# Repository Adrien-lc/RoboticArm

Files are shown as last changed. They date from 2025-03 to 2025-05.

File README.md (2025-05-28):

# Robotic Arm






<p float="left">
  
</p>

## Overview

This Robotic Arm is designed to perform simple to complex manipulative tasks, enabling the implementation of AI models. The arm is scaled to human proportions and designed to be cost-effective, with all parts 3D printed.

The arm can be used both vertically, like a human arm, or horizontally, like a traditional DOF robot. It only needs to be connected to a computer through the USB-C port.

<p float="left">
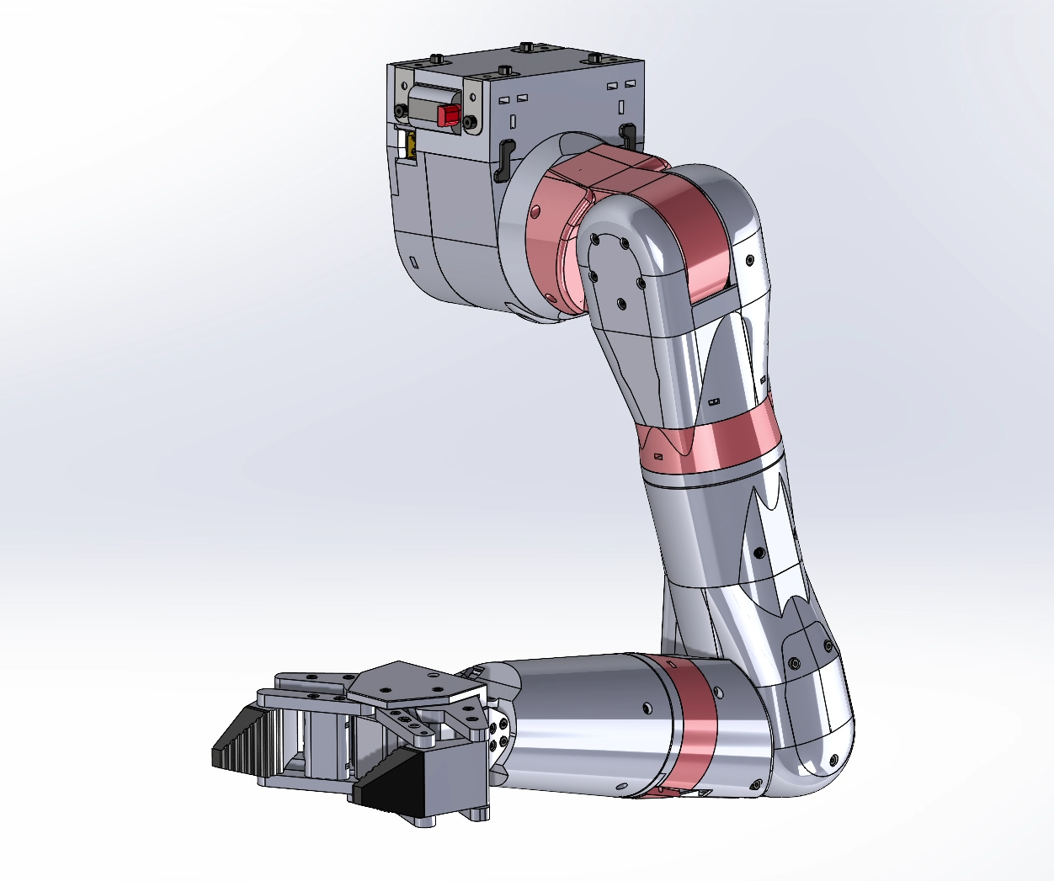
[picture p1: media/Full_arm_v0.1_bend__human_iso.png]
  
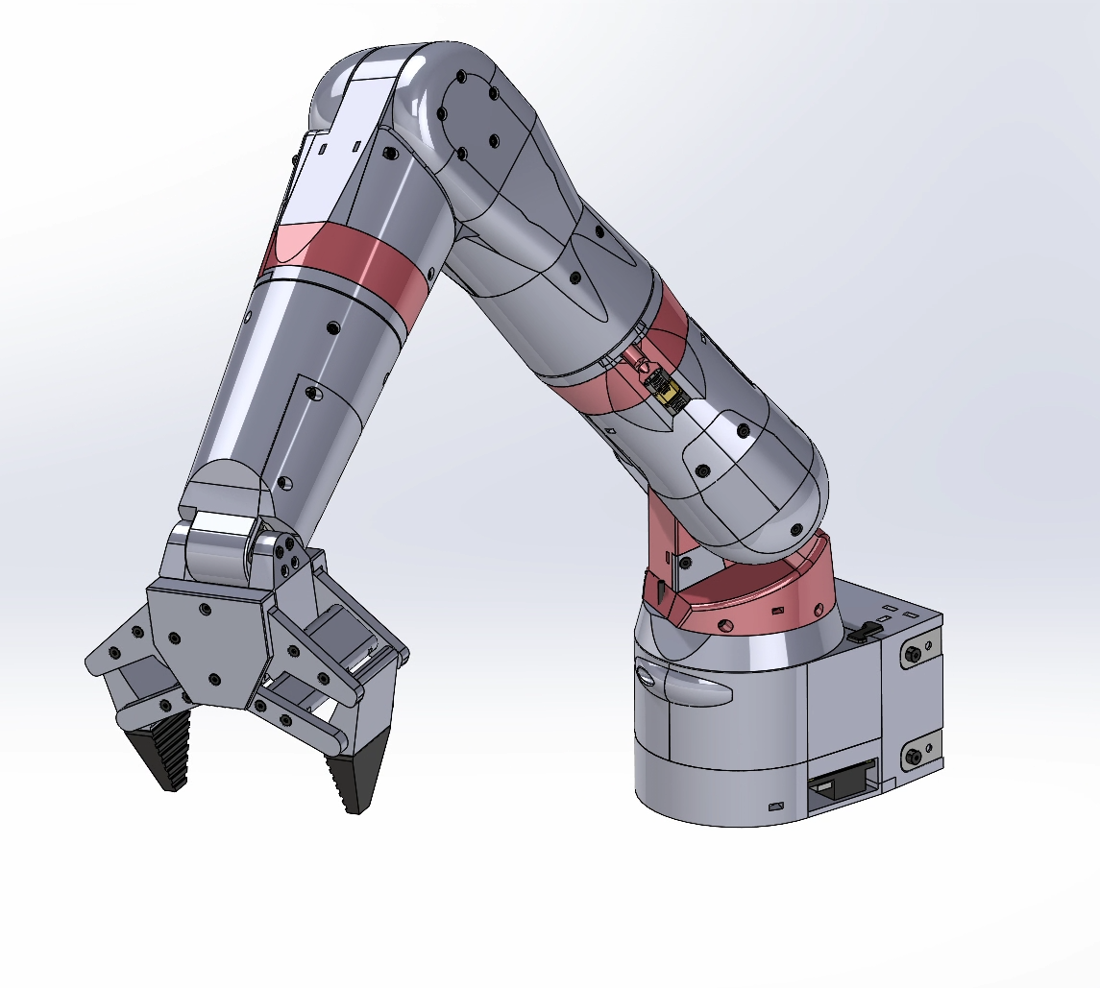
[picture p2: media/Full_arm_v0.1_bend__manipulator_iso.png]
  
</p>

## Sourcing Parts

Detailed part costs and links are shown below. Some links may provide more than the necessary quantity. You can find the complete Bill of Materials (BOM) in the repository files. 

Please note, you need to add the cost of the 3D printed parts to this list.

> Only EU costs and availability have been calculated.

### Parts to buy : 

| Description | Supplier | Quantity | Unit Price (EUR) | Total Price (EUR) | Link |
|---|---|---|---|---|---|
| Servo Feetech STS3215 | Alibaba | 7 | 13 | 91 | [Alibaba](https://docs.google.com/spreadsheets/d/1NSq1UUoz3DjgiEBvVC6gFn5Jqz1jVz-hb513ZOTMuxQ/edit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) |
| Waveshare Serial Bus Servo Driver Board | Amazon | 1 | 11.99 | 11.99 | [Amazon](https://www.amazon.fr/dp/B0CJ6TP3TP) |
| LiPo Roaringtop 2200mAh 35C, 2pcs | Amazon | 1 | 32.1 | 32.1 | [Amazon](https://www.amazon.fr/dp/B08H82KFS6/ref=twister_B09YHFFBK1?_encoding=UTF8&th=1) |
| Universal Lithium Grease | Amazon | 1 | 7.99 | 7.99 | [Amazon](https://www.amazon.fr/dp/B008ETHDPO) |
| Hex Screw M3 Socket Cap, Box | Amazon | 1 | 10.59 | 10.59 | [Amazon](https://www.amazon.fr/dp/B093GNHWKR) |
| Bearing 20x27x4, 6704 2RS, 5pcs | Aliexpress | 1 | 4.61 | 4.61 | [Aliexpress](https://fr.aliexpress.com/item/1005006822777675.html) |
| Bearing 8x16x5, 688ZZ, 10pcs | Aliexpress | 1 | 1.75 | 1.75 | [Aliexpress](https://fr.aliexpress.com/item/1005007235103277.html) |
| Bearing 40x52x7, 6808-2RS, 2pcs | Aliexpress | 2 | 3.51 | 7.02 | [Aliexpress](https://fr.aliexpress.com/item/1005007420073930.html) |
| Bearing 15x21x4, 6702ZZ, ABEC 1, 10pcs | Aliexpress | 2 | 3.43 | 6.86 | [Aliexpress](https://fr.aliexpress.com/item/4000909621264.html) |
| Bearing 50x65x7, 6810-2RS, 2pcs | Aliexpress | 2 | 5.09 | 10.18 | [Aliexpress](https://fr.aliexpress.com/item/1005007420073930.html) |
| Wire AWG16 3 Core, 3m | Aliexpress | 1 | 10.39 | 10.39 | [Aliexpress](https://fr.aliexpress.com/item/1005006405984242.html) |
| Hex Socket M3 Countersunk Flat Head Screw, 8mm, 50pcs | Aliexpress | 1 | 1.66 | 1.66 | [Aliexpress](https://fr.aliexpress.com/item/4001199728978.html) |
| Hex Socket M3 Countersunk Flat Head Screw, 10mm, 50pcs | Aliexpress | 1 | 1.75 | 1.75 | [Aliexpress](https://fr.aliexpress.com/item/4001199728978.html) |
| Hex Socket M3 Countersunk Flat Head Screw, 12mm, 50pcs | Aliexpress | 1 | 1.84 | 1.84 | [Aliexpress](https://fr.aliexpress.com/item/4001199728978.html) |
| Hex Socket M3 Countersunk Flat Head Screw, 16mm, 50pcs | Aliexpress | 1 | 2.04 | 2.04 | [Aliexpress](https://fr.aliexpress.com/item/4001199728978.html) |
| Dowel Pin M2, 20mm, 20pcs | Aliexpress | 1 | 1.3 | 1.3 | [Aliexpress](https://fr.aliexpress.com/item/1005007218328914.html) |
| Dowel Pin M3, 30mm, 20pcs | Aliexpress | 1 | 2.69 | 2.69 | [Aliexpress](https://fr.aliexpress.com/item/1005007023343232.html) |
| Dowel Pin M3, 25mm, 20pcs | Aliexpress | 1 | 2.55 | 2.55 | [Aliexpress](https://fr.aliexpress.com/item/1005007023343232.html) |
| Dowel Pin M3, 16mm, 20pcs | Aliexpress | 1 | 2.06 | 2.06 | [Aliexpress](https://fr.aliexpress.com/item/1005007023343232.html) |
| AMASS MR30 Pair Male+Female, 10pcs | Aliexpress | 1 | 6.61 | 6.61 | [Aliexpress](https://fr.aliexpress.com/item/1005005485789207.html) |
| Heat Shrink Tube, Box 127pcs | Aliexpress | 1 | 2.24 | 2.24 | [Aliexpress](https://fr.aliexpress.com/item/1005001787291963.html) |
| Allen Hexagon Head Screws M4 20mm, 10pcs | Aliexpress | 1 | 1.36 | 1.36 | [Aliexpress](https://fr.aliexpress.com/item/32442183034.html) |
| Allen Hexagon Head Screws M4 40mm, 10pcs | Aliexpress | 1 | 1.88 | 1.88 | [Aliexpress](https://fr.aliexpress.com/item/32442183034.html) |
| M4 Nuts Hexa, 25pcs | Aliexpress | 1 | 1.38 | 1.38 | [Aliexpress](https://fr.aliexpress.com/item/32977174437.html) |
| Hex Socket M2.5 Countersunk Flat Head Screw, 12mm, 50pcs | Aliexpress | 1 | 1.65 | 1.65 | [Aliexpress](https://fr.aliexpress.com/item/4001199728978.html) |
| Hex Socket M3 Countersunk Flat Head Screw, 25mm, 50pcs | Aliexpress | 1 | 2.59 | 2.59 | [Aliexpress](https://fr.aliexpress.com/item/4001199728978.html) |
| Hex Socket M3 Socketcap Head Screw, 45mm, 50pcs | Aliexpress | 1 | 3.80 | 3.80 | [Aliexpress](https://fr.aliexpress.com/item/32442183034.html) |
| XT60 Male Connector | Aliexpress | 1 | 1.59 | 1.59 | [Aliexpress](https://fr.aliexpress.com/item/1005006840459578.html) |
| Lipo Battery Charger | Aliexpress | 1 | 5.01 | 5.01 | [Aliexpress](https://fr.aliexpress.com/item/1005007620618797.html) |
| MR30 male and female connector, 10pcs | Aliexpress | 1 | 6.59 | 7.99 | [Aliexpress](https://fr.aliexpress.com/item/1005005485789207.html) |
| **Total** |  |  |  | **246.96** | |

> Make sure the AWG 16, 3-core wire outside diameter is equal to or less than 7mm.

### 3D Printed Parts

All the 3D printed parts can be found in the `/STEP` folder.  For main assembly, open `Bionic_arm.STEP`
Parts have been tested with an Artillery SW-X4 Plus printer.

## Specifications

This arm is first designed as a human arm. It has a 1:1 scale and the same joint amplitude :

- The arm needs to be able to lift a 500g object.
- End-effector position error must be < 1 cm.
- The arm must be able to pick up an object from any orientation within its kinematic workspace.
- Actuator velocity must be fast enough to perform a task at a reasonable speed. Full amplitude < 4s.

### Joint Amplitude:

| Joint | Min  | Max  | Amplitude |
|---|---|---|---|
| Shoulder Y | -90  | 180  | 270 |
| Shoulder X | -20  | 150  | 170 |
| Upper Z | -180 | 90 | 270 |
| Elbow Y | -60  | 110  | 170 |
| Forearm Z  | -90  | 90 | 180 |
| Wrist Y | -60  | 60 | 120 |

A first draft was made in Isaac Sim to determine the required specifications for the actuators:
- Joints were placed in the same positions as a human arm.
- The final robot mass was approximated for each rigid body.
- A 500g load was added to the gripper mass to simulate the payload.

Lula RMPflow controller is used, with different positions given while joint effort and velocity are recorded:

<p float="left">
  
</p>

<p float="left">
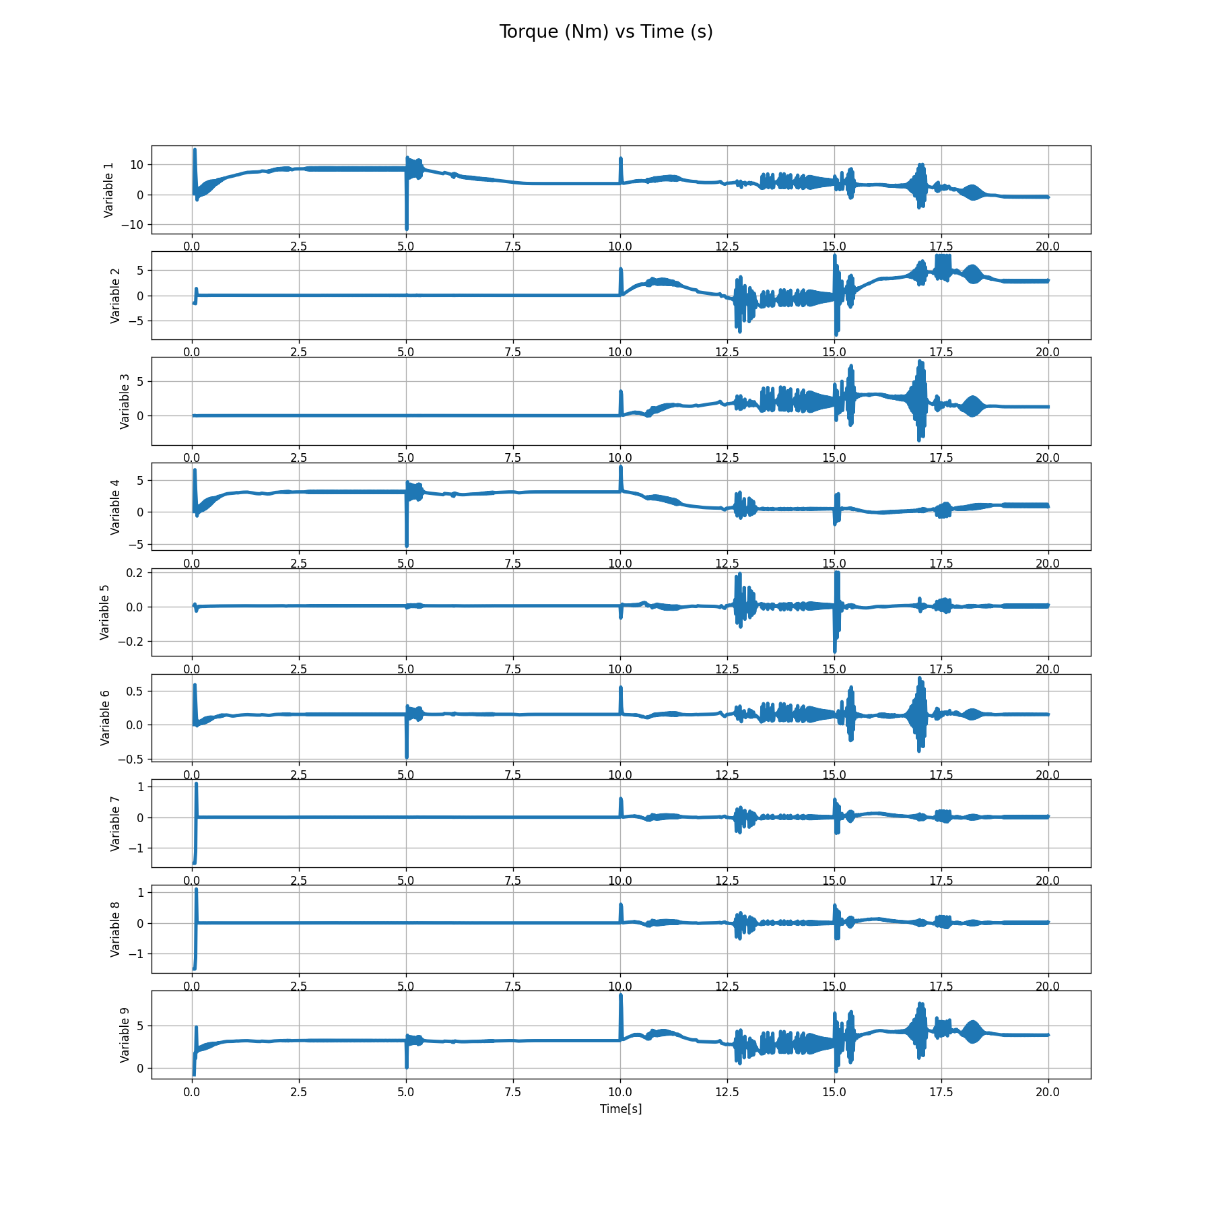
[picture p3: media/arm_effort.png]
  
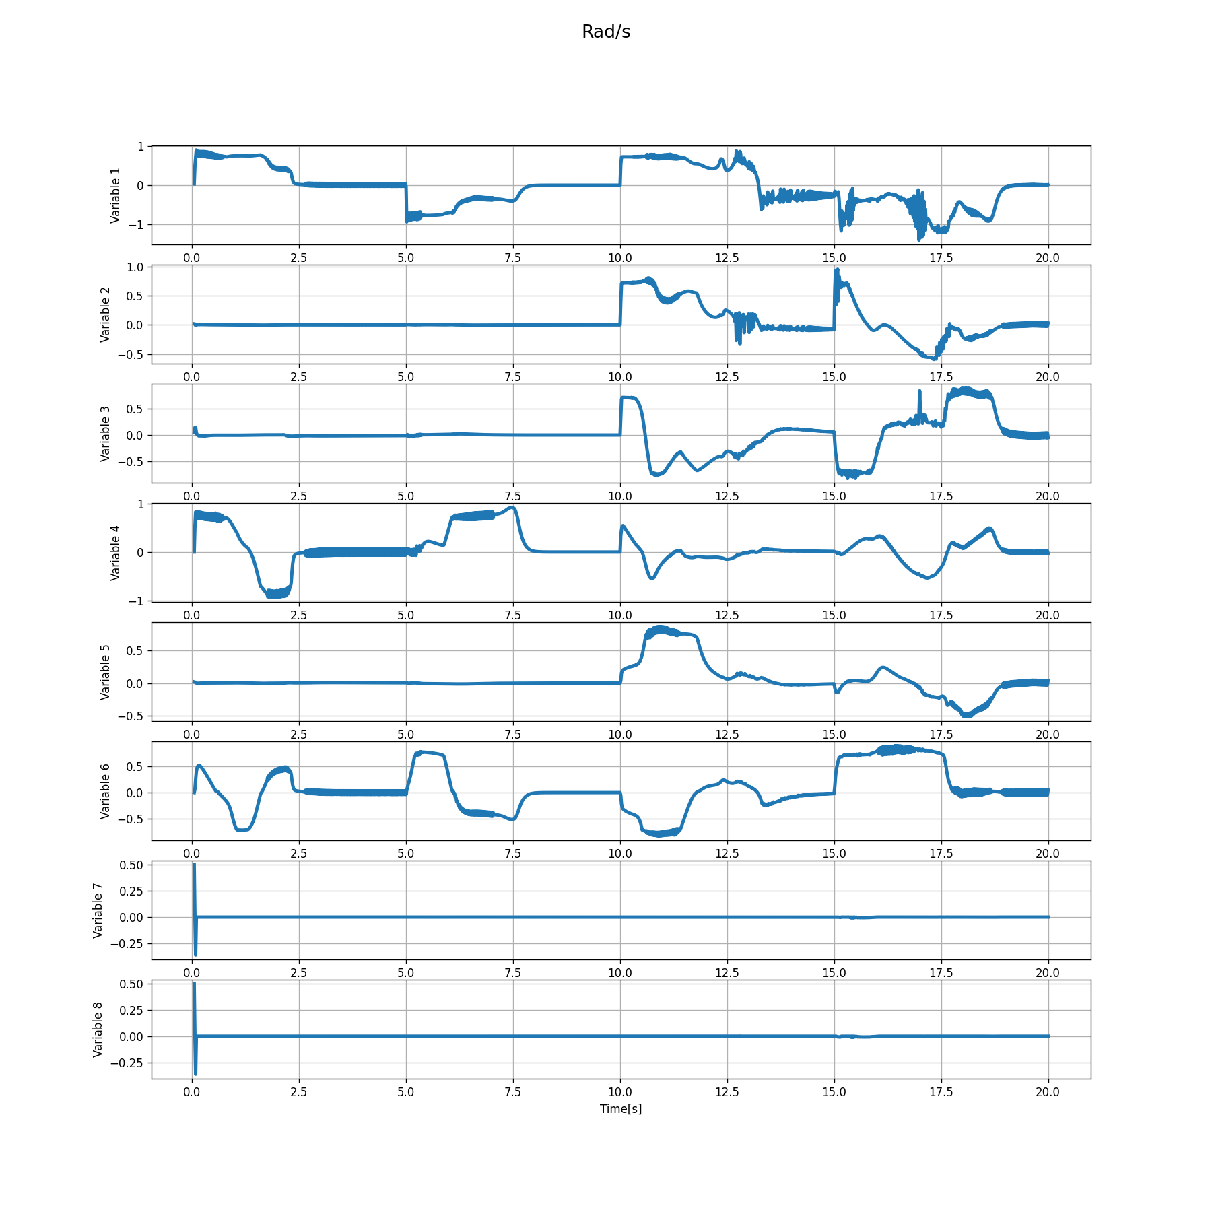
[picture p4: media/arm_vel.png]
  
</p>

### The minimum actuator specifications required are:
- **10 Nm** for the first shoulder joint, **5 Nm** for the rest.
- **≥ 1 rad/s** velocity.

**STS3215** serial servo (3 Nm, 5.5 rad/s, 12V) has been selected for all the joints.

Serial servo allows easier wire management, position/velocity/torque feedback, and features a multi-turn encoder.  
A cycloidal drive will be coupled to the STS servo to achieve the desired torque.

## Cycloid Drive

The gearbox will be used with the Feetech STS3215 servomotors (30 kg·cm, 52 rpm / 5.5 rad/s), with a desired **5:1** gear ratio.  
The shape of the rotor and stator has been tuned using the Python script `cycloid_tuning.py`:  

| Parameter | Value | Description |
|---|---|---|
| R | 36 mm | Pitch radius of fixed ring pins |
| E | 2 mm | Eccentricity offset |
| Rr | 8 mm | Ring pin radius |
| N | 6 | Number of ring pins |
| Sharpness | 6.5 mm  | Pitch angle around stator ring pins |

<p float="left">
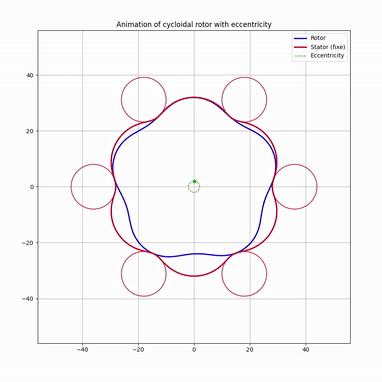
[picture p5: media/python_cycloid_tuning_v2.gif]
  
</p>

This design aims to achieve the best torque distribution and minimize backlash.  
As both rotors and the housing are **3D printed**, a **three-rotor design** has been chosen.  
The Cycloid assembly can be open with `Cycloid_drive_default.STEP` in the `/STEP` folder.  

<p float="left">
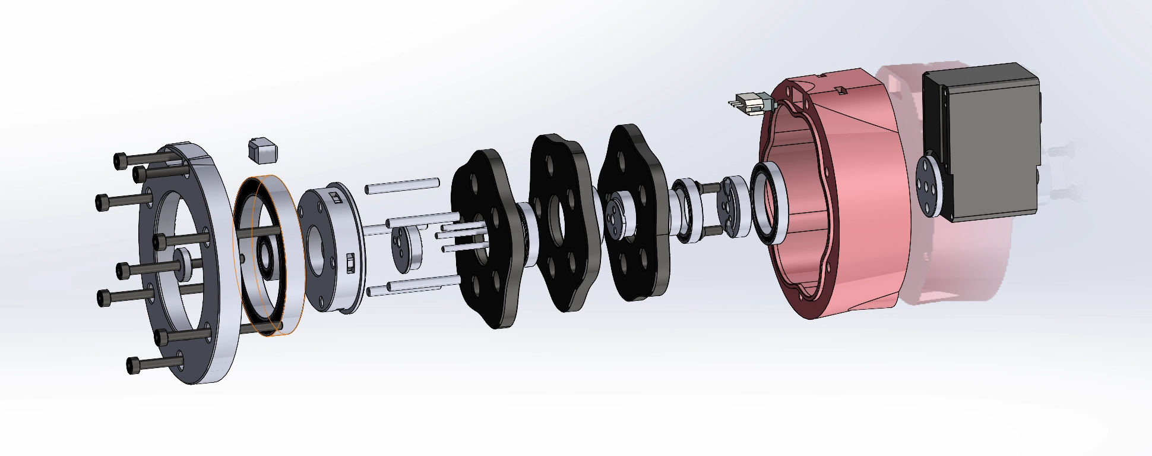
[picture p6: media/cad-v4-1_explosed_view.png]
  
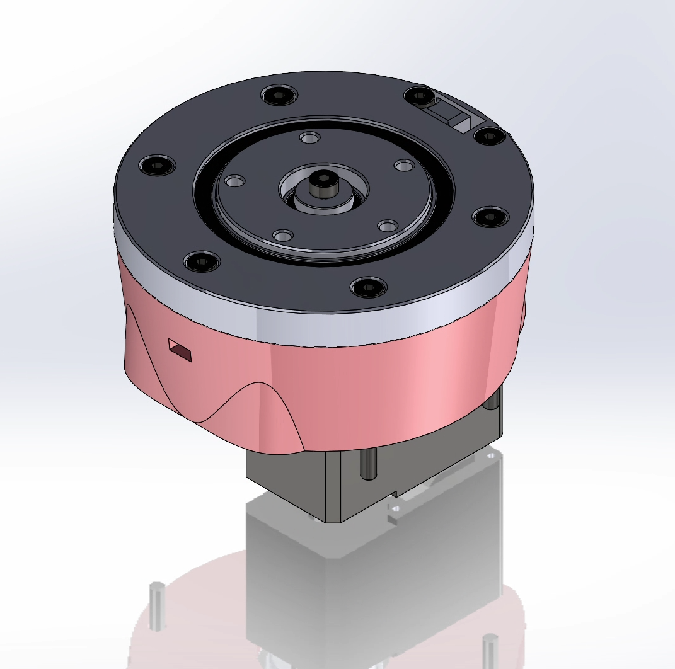
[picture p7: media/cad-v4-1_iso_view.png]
  
</p>

A load test has been conducted to measure output torque, speed, backlash, and efficiency:  

- **Output torque**: 9 Nm  
- **Output velocity**: 1.1 rad/s  
- **Backlash after load**: 0.5°  
- **Efficiency**: (9/3)/5 = **0.6** *(test were conducted with grease)*  

## Assembly

Use the main Assembly File for the main assembly `Bionic_arm.STEP`

**Base component management :**

<p float="left">
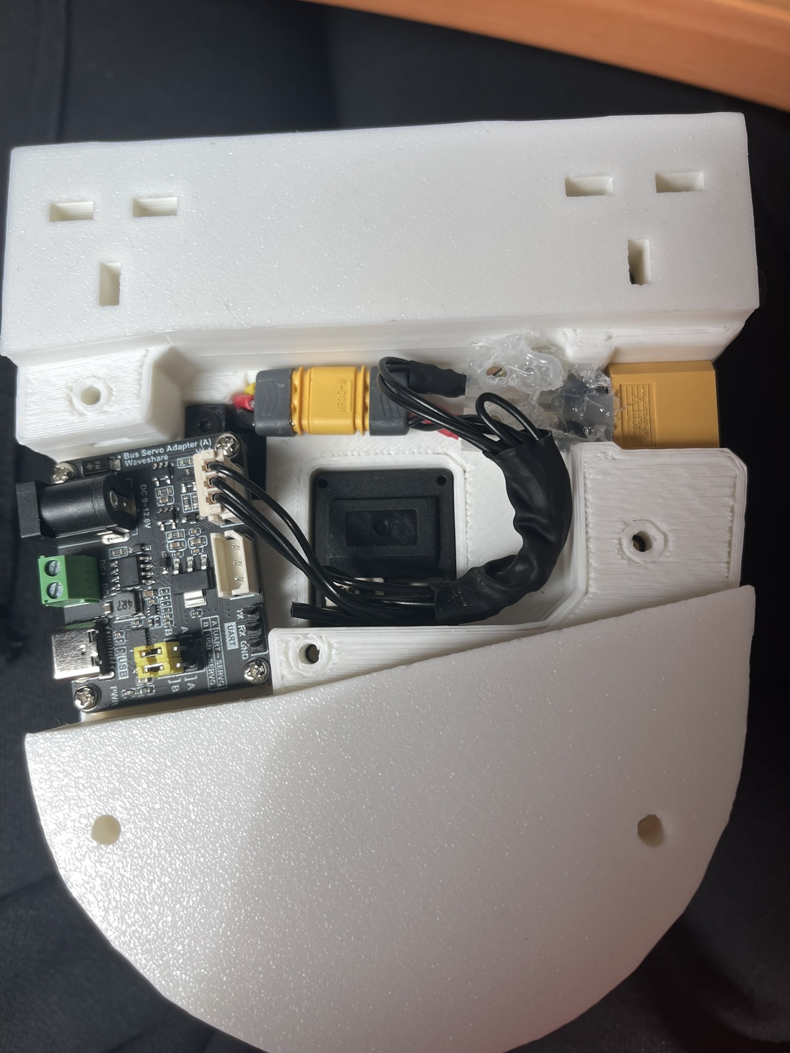
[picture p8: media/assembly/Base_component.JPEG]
  
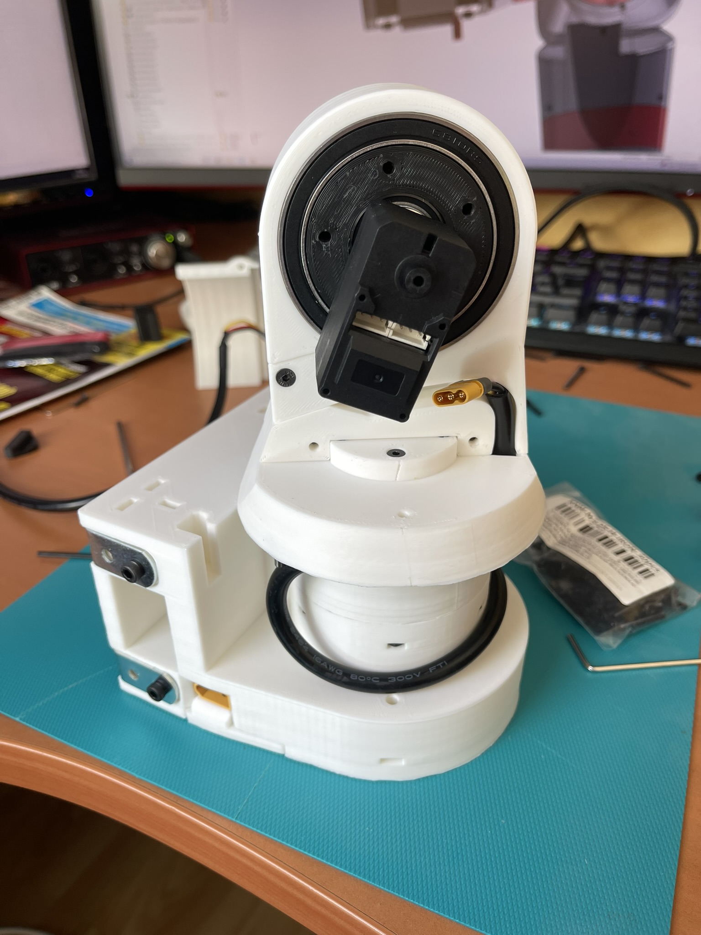
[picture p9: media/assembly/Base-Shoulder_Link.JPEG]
  
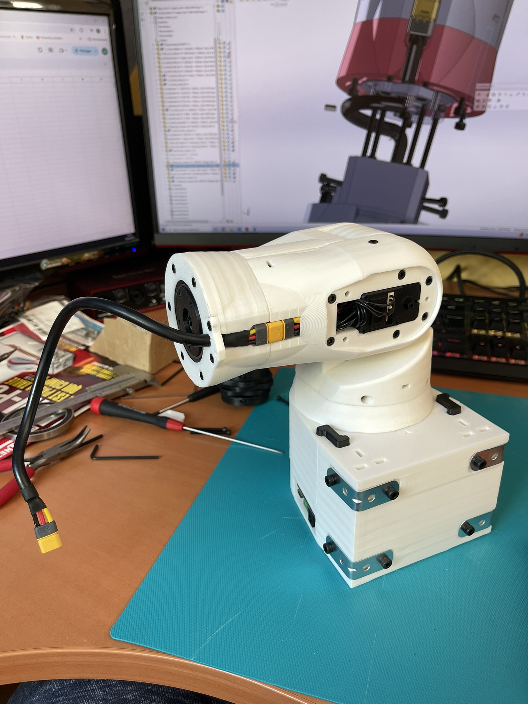
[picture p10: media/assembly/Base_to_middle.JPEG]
  

</p>

> Wire length must be calculated by doing a full amplitude on the joint before soldering it.

**Upper link Wire Management :**

<p float="left">
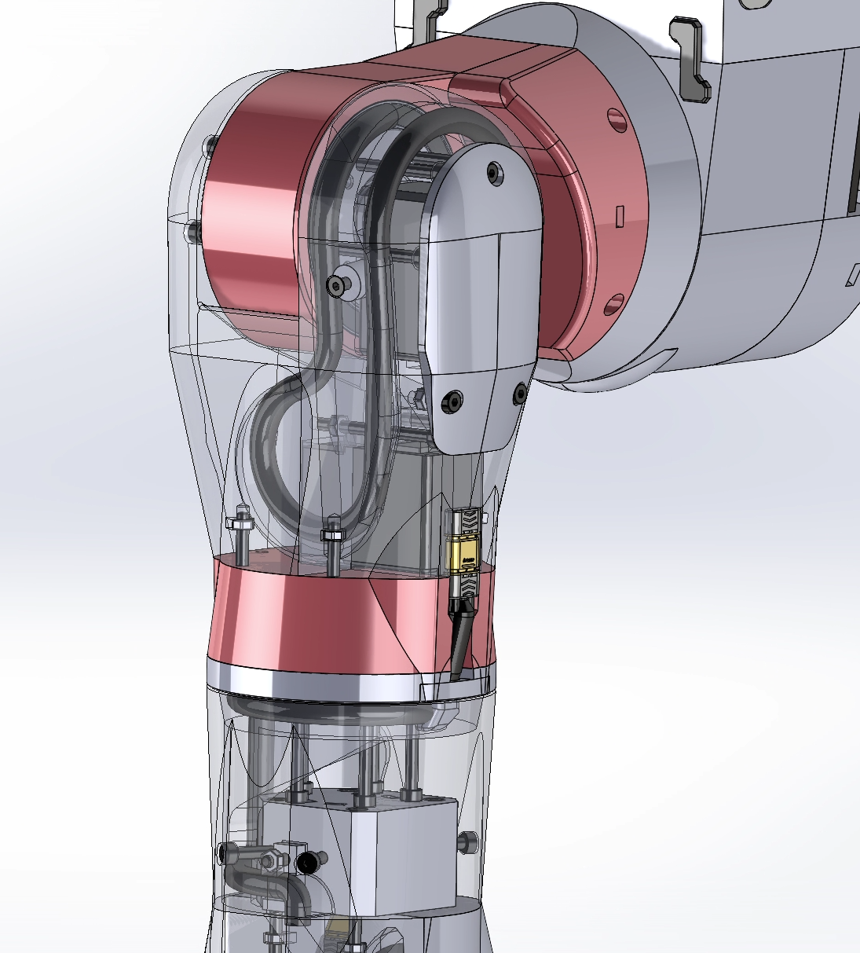
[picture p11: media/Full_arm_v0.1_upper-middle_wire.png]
  
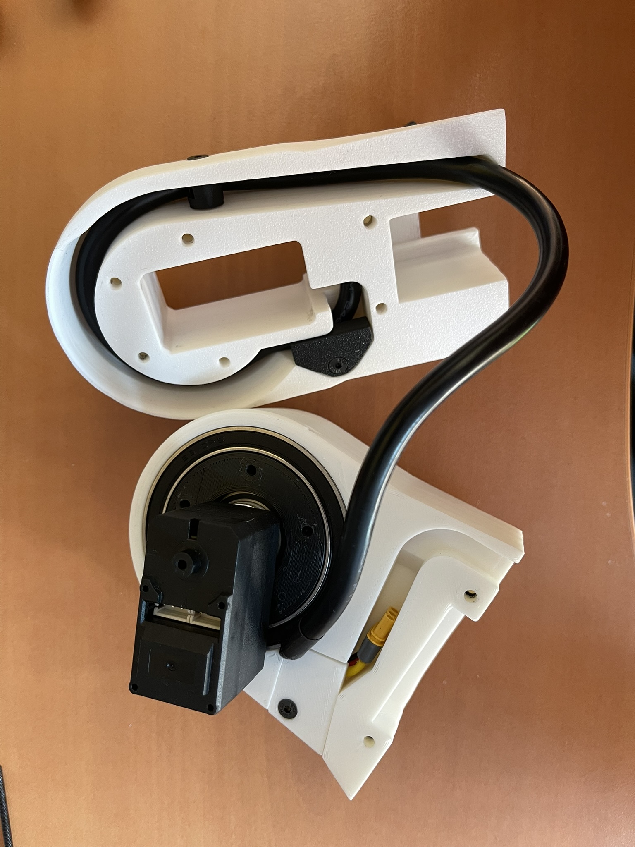
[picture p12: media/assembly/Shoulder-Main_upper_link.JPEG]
  
</p>

> Same wire management for Elbow link

**Fore arm and Wrist link**

<p float="left">
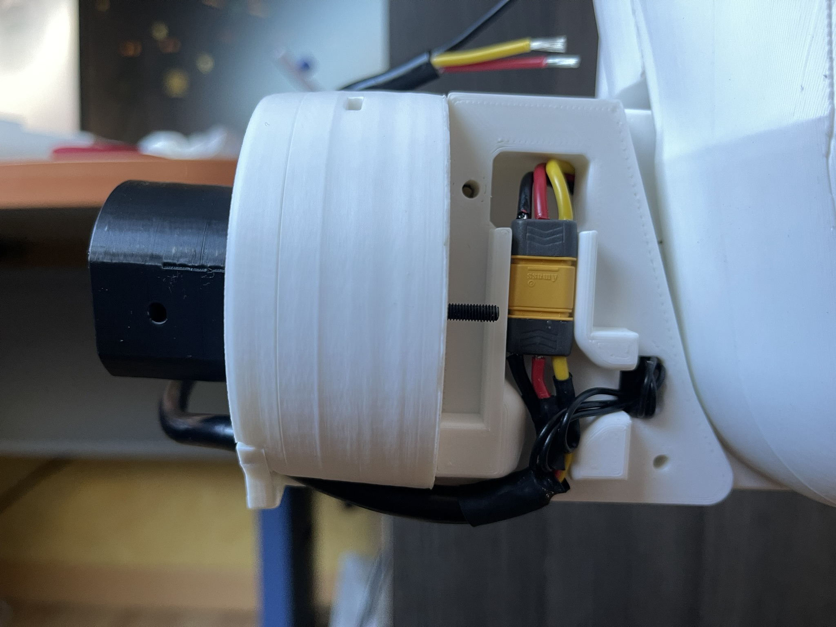
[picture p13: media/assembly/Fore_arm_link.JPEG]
  
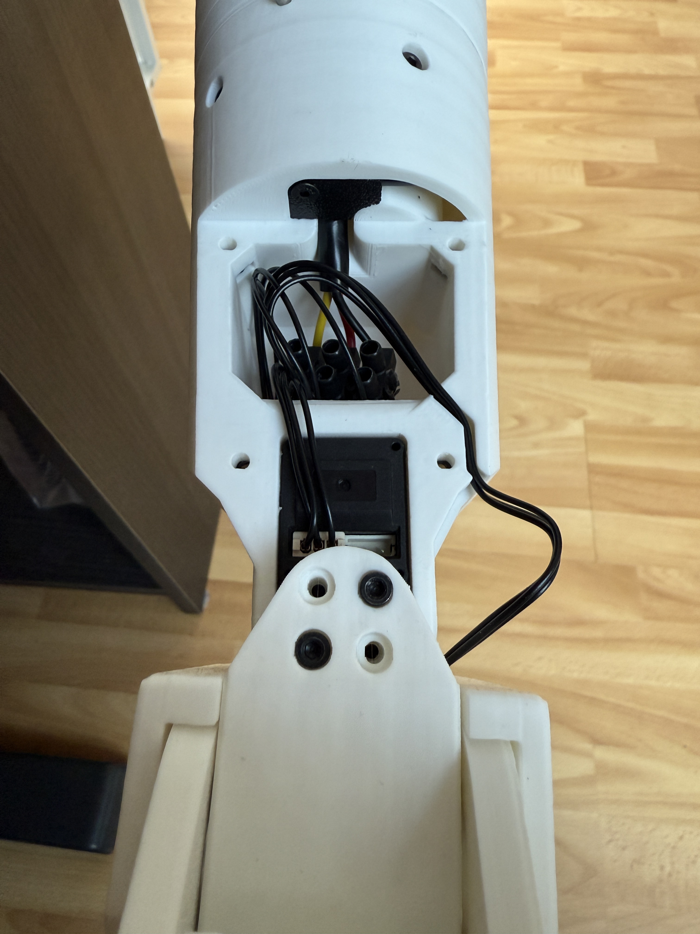
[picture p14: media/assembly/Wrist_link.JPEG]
  
</p>

## IsaacSim

IsaacSim USD file can be found in /isaacSim/USD

### Manipulation Tasks :

In this task, IsaacSim lead the real arm using Lula RMPFlow controller. Current positions and velocities of each joint are sent to the robot in real time :

<p float="left">
  
</p>

### RL (coming soon):

Reinforcement learning model with IsaacLab.

## Software :

<p>Servo motor-related features, such as calibration and serial addressing, were inspired by scripts from <a href="https://github.com/huggingface/lerobot"> Lerobot repository.</a></p>

IsaacSim instance is hosted on a cloud machine, and communication with the local system is handled via a TCP socket, as illustrated in the diagram below. Currently, TCP communication is unidirectional—from IsaacSim to the robot—due to internet latency constraints.

<p float="left">
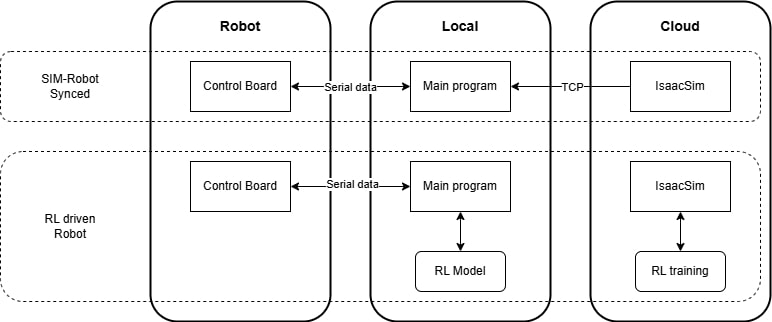
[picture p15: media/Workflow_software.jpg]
  
</p>

The local system runs a main control program , which orchestrates motor connection, calibration routines, overload protection, position safety mechanisms, and TCP communication. All the scripts are written in Python

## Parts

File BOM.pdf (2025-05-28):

ITEM NO. | PART NUMBER | SW-Configuration Name(Configuration Name) | Source | toBuy | DESCRIPTION | QTE
1 | cycloid_housing | default | 3D Print | | | 1
2 | planche | default | home | | | 1
3 | base_housing | default | 3D Print | | | 1
4 | base_axis | default | Printed | | | 1
5 | wire_cover_base_2 | default | Printed | | | 1
6 | cable_pulley | base | Aliexpress | Yes | awg 16 wire, 3 core | 1
7 | roulement | 40x52x7 | Aliexpress | Yes | Bearings | 3
8 | cover_housing | left | Printed | | | 1
9 | cover_housing | right | Printed | | | 1
10 | hex_m3_custom | flat_25mm | Aliexpress | Yes | Screw m3 hexa | 9
11 | nut_m4_hex_custom | default | Aliexpress | Yes | Nut m4 hexa | 12
12 | hex_m4_custom | socketcap_20mm | Aliexpress | Yes | screw M4 hexa | 4
13 | bracket_30x30 | default | | Yes | steel bracket 30x30m m4 | 4
14 | hex_m4_custom | socketcap_40mm | Aliexpress | Yes | screw M4 hexa | 4
15 | hex_m4_custom | socketcap_16mm | Aliexpress | Yes | screw M4 hexa | 4
16 | hex_m3_custom | socketcap_25mm | Aliexpress | Yes | Screw m3 hexa | 10
17 | nut_m3_hex_custom | default | Aliexpress | Yes | Nut hex M3 | 123
18 | hex_m3_custom | socketcap_20mm | Aliexpress | Yes | Screw m3 hexa | 14
19 | wire_cover_base | default | 3D Print | | | 1
20 | hex_m3_custom | flat_16mm | Aliexpress | Yes | Screw m3 hexa | 20
21 | hex_m3_custom | socketcap_30mm | Aliexpress | Yes | Screw m3 hexa | 6
22 | hex_m3_custom | socketcap_16mm | Aliexpress | Yes | Screw m3 hexa | 19
23 | hex_m3_custom | flat_12mm | Aliexpress | Yes | Screw m3 hexa | 9
24 | cycloid_housing | housing_rotation_shoulder | 3D Print | | | 1
25 | cycloid_housing | top_shoulder | 3D Print | | | 1
26 | cycloid_housing | bot_shoulder | 3D Print | | | 1
27 | cycloid_housing | housing_rotation_cache | 3D Print | | | 2
28 | ASM, Amass MR30 mated pair | default | Aliexpress | Yes | MR30 male and female connector | 6
29 | cycloid_housing | upper_arm | 3D Print | | | 1
30 | cycloid_housing | housing_rotation_elbow | 3D Print | | | 3
31 | middle_arm | default | 3D Print | | | 1
32 | cycloid_housing | fore_arm | 3D Print | | | 1
33 | servoFeetechSTS3215 | Default | Alibaba | Yes | Feetech STS3215 serial servo motor, 30kg.cm, 52rpm | 7

34 | servo_diskpin | default | feetech STS3215 | | | 8
35 | hex_m3_custom | flat_8mm | Aliexpress | Yes | Screw m3 hexa | 10
36 | cycloid_shaft_p1 | housing_rotation | 3D Print | | | 2
37 | cycloid_shaft_p2 | default | 3D Print | | | 10
38 | cycloid_shaft_p2 | top | 3D Print | | | 5
39 | cycloid_shaft_p3 | default | 3D Print | | | 5
40 | cycloid_shaft_p4 | default | 3D Print | | | 5
41 | roulement | 20x27x4 | Aliexpress | Yes | Bearings | 5
42 | roulement | 15x21x4 | Aliexpress | Yes | Bearings | 15
43 | roulement | 8x16x5 | Aliexpress | Yes | Bearings | 7
44 | cycloid_rotor | 240 | 3D Print | | | 5
45 | cycloid_rotor | 120 | 3D Print | | | 5
46 | cycloid_outputdisk | housing_rotation | 3D Print | | | 2
47 | dowel_pin_custom | M3x30 | Aliexpress | Yes | Dowel pin | 10
48 | roulement | 50x65x7 | Aliexpress | Yes | Bearings | 4
49 | hex_m3_custom | socketcap_40mm | Aliexpress | Yes | Screw m3 hexa | 17
50 | cycloid_outputdisk | housing_rotation_bot | 3D Print | | | 2
51 | dowel_pin_custom | M2x20 | Aliexpress | Yes | Dowel pin | 11
52 | Upper_arm | part1 | 3D Print | | | 1
53 | Upper_arm | part2 | 3D Print | | | 1
54 | Upper_arm | part3 | 3D Print | | | 2
55 | cable_pulley | upper_arm | Aliexpress | Yes | awg 16 wire, 3 core | 2
56 | Amass MR30-shroud_default | default | Aliexpress | Yes | | 12
57 | hex_m3_custom | socketcap_35mm | Aliexpress | Yes | Screw m3 hexa | 18
58 | hex_m3_custom | socketcap_10mm | Aliexpress | Yes | Screw m3 hexa | 6
59 | pulley | default | Printed | | | 2
60 | cycloid_shaft_p1 | default | 3D Print | | | 3
61 | cycloid_outputdisk | default | 3D Print | | | 3
62 | dowel_pin_custom | M3x25 | Aliexpress | Yes | Dowel pin | 15
63 | top_housing | fore_arm | Printed | | | 1
64 | top_housing | cache_cable_upper | Printed | | | 1
65 | cycloid_rotor | default | 3D Print | | | 5
66 | middle_arm | inside | 3D Print | | | 1
67 | cable_pulley | middle_arm | Aliexpress | Yes | awg 16 wire, 3 core | 1

68 | wire_cover_middle_arm | default | 3D Print | | | 1
69 | Upper_arm | elbow_part1 | 3D Print | | | 1
70 | Upper_arm | elbow_part2 | 3D Print | | | 1
71 | cycloid_housing | bot_elbow | 3D Print | | | 1
72 | cycloid_housing | top_elbow | 3D Print | | | 1
73 | top_housing | upper_arm | Printed | | | 1
74 | top_housing | cache_cable_fore | Printed | | | 1
75 | fore_arm | part1 | 3D Print | | | 1
76 | fore_arm | wire_cover | 3D Print | | | 1
77 | fore_arm | part2 | 3D Print | | | 1
78 | fore_arm | part3 | 3D Print | | | 1
79 | cable_pulley | fore_arm | Aliexpress | Yes | awg 16 wire, 3 core | 1
80 | gripper_gear | left_top | 3D Print | | | 1
81 | gripper_base | default | 3D Print | | | 1
82 | gripper_stick | default | 3D Print | | | 4
83 | gripper_finger | default | 3D Print | | | 2
84 | gripper_gear | right_top | 3D Print | | | 1
85 | servo_diskpin | non_drived | feetech STS3215 | | | 1
86 | gripper_gear | right_bot | 3D Print | | | 1
87 | top_gripper | default | 3D Print | | | 1
88 | dowel_pin_custom | M3x12 | Aliexpress | Yes | Dowel pin | 9
89 | bearing_shaft | default | 3D Print | | | 2
90 | top_gripper | bot | 3D Print | | | 1
91 | gripper_gear_middle | default | 3D Print | | | 2
92 | hex_m3_custom | flat_10mm | Aliexpress | Yes | Screw m3 hexa | 8
93 | gripper_gear_middle | stick | 3D Print | | | 2
94 | gripper_gear | left_bottom | 3D Print | | | 1
95 | wire_cover_gripper | default | 3D Print | | | 1
96 | gripper_finger | tpu | 3D Print | | | 2
97 | dowel_pin_custom | M3x16 | Aliexpress | Yes | Dowel pin | 4
98 | base_housing | bot | 3D Print | | | 1
99 | RoaringTop_2200mah | default | Amazon | Yes | 2200mha lipo battery roaringtop | 1
100 | top_housing | default | Printed | | | 1
101 | hex_m3_custom | socketcap_45mm | Aliexpress | Yes | Screw m3 hexa | 8

102 | XT60_male_connector | default | Aliexpress | Yes | XT60 male connector | 1
103 | WaveShare_Bus_Servo_DriverBoard | Défaut | Amazon | Yes | WaveShare serial bus servo adaptater board | 1
104 | hex_m2-5_custom | flat_12mm | Aliexpress | Yes | self_tapping Screw M2.6 | 2
105 | housing_lock | default | 3D Print | | | 2
106 | hex_m3_custom | socketcap_12mm | Aliexpress | Yes | Screw m3 hexa | 16
107 | wire_cover_mainlink | default | Printed | | | 2
108 | dowel_pin_custom | M3x10 | Aliexpress | Yes | Dowel pin | 2
109 | dowel_pin_custom | M3x6 | Aliexpress | Yes | Dowel pin | 4

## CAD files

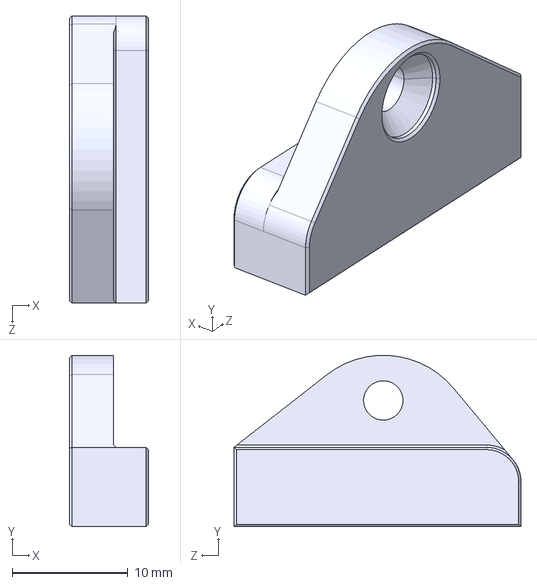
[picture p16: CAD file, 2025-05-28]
STEP/wire_cover_mainlink_default.STEP
6.80 x 14.8 x 24.8 mm

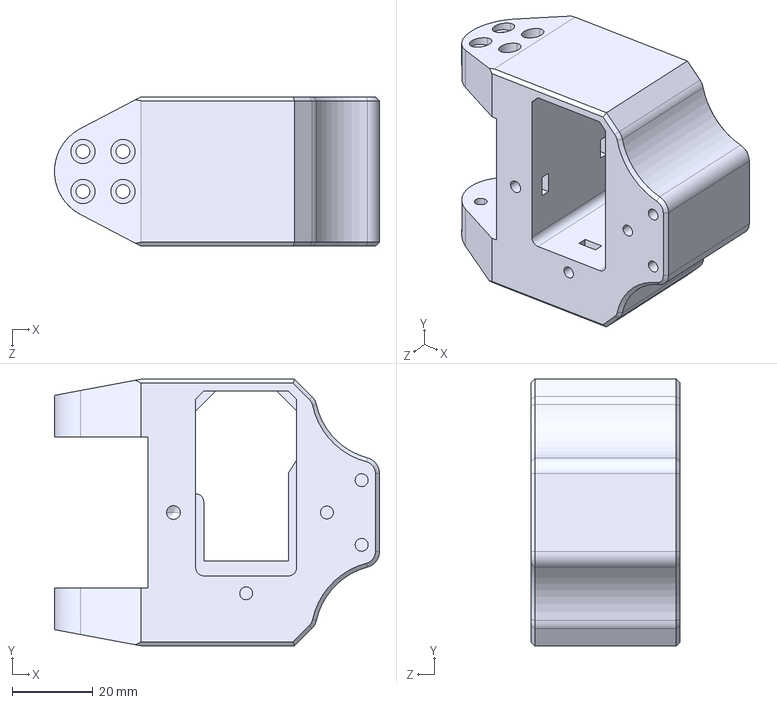
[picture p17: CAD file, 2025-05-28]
STEP/gripper_base_default.STEP
80.4 x 66.0 x 37.0 mm

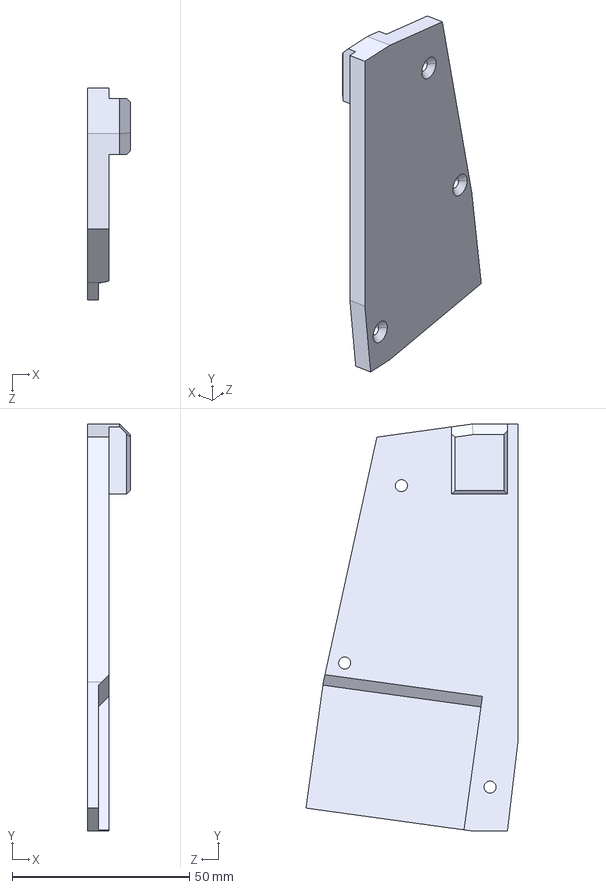
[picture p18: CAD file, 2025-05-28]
STEP/base_housing_bot.STEP
12.0 x 114.8 x 59.8 mm

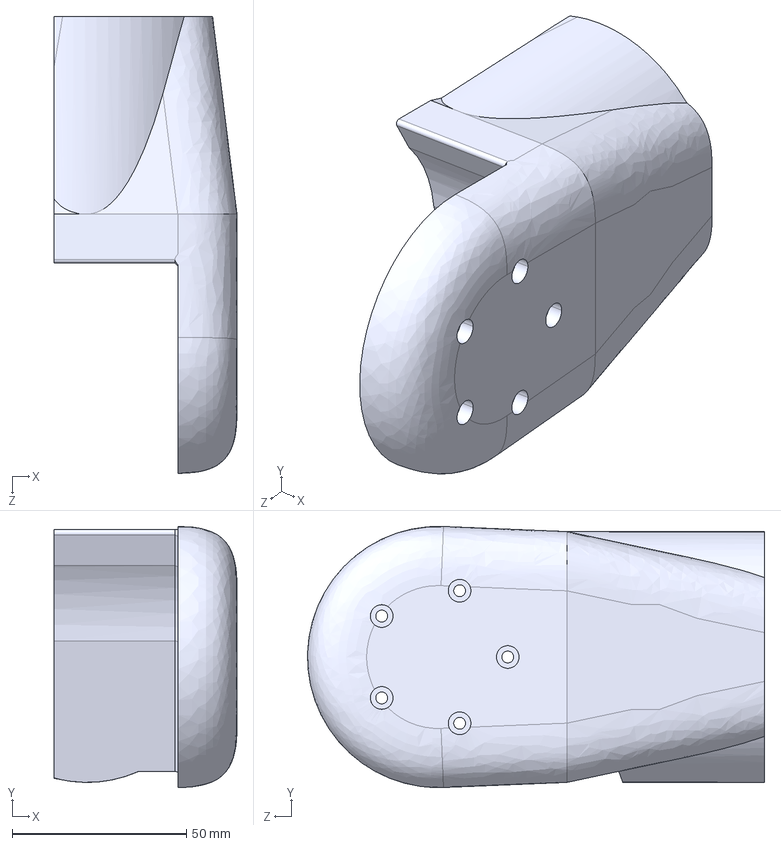
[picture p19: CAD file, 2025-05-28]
STEP/Upper_arm_elbow_part1.STEP
52.5 x 74.9 x 131.2 mm

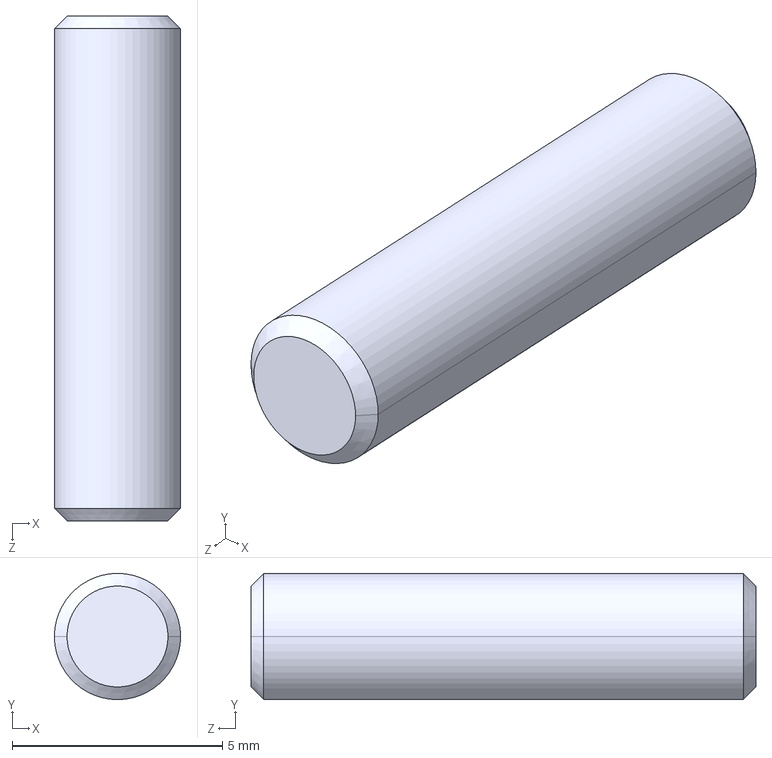
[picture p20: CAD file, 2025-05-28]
STEP/dowel_pin_custom_M3x12.STEP
3.00 x 3.00 x 12.0 mm

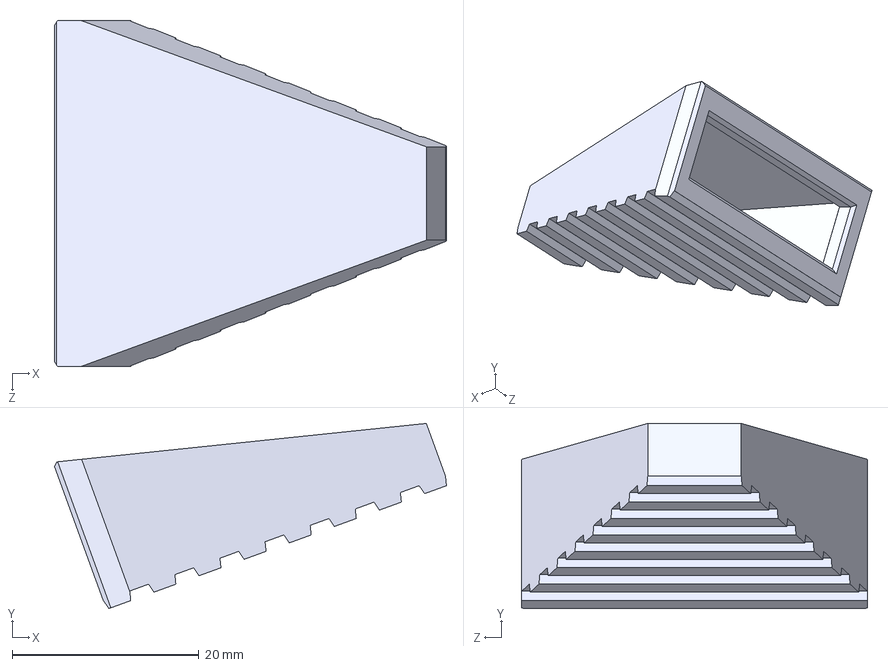
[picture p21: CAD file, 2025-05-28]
STEP/gripper_finger_tpu.STEP
42.0 x 19.8 x 37.0 mm

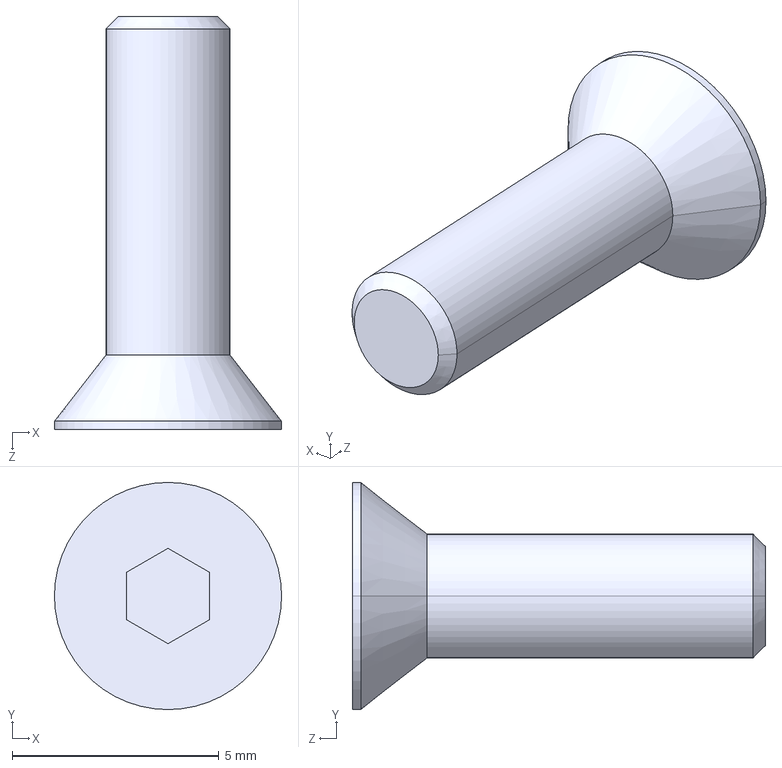
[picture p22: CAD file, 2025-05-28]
STEP/hex_m3_custom_flat_10mm.STEP
5.50 x 5.50 x 10.0 mm

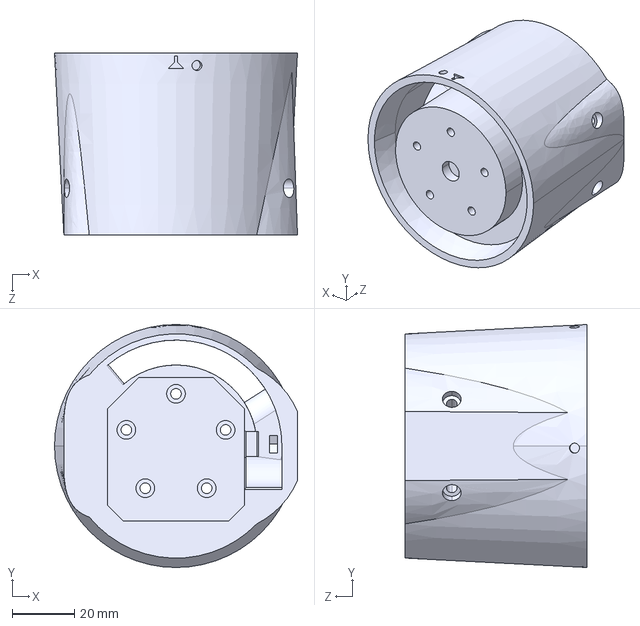
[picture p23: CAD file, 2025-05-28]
STEP/middle_arm_default.STEP
78.0 x 78.0 x 58.4 mm

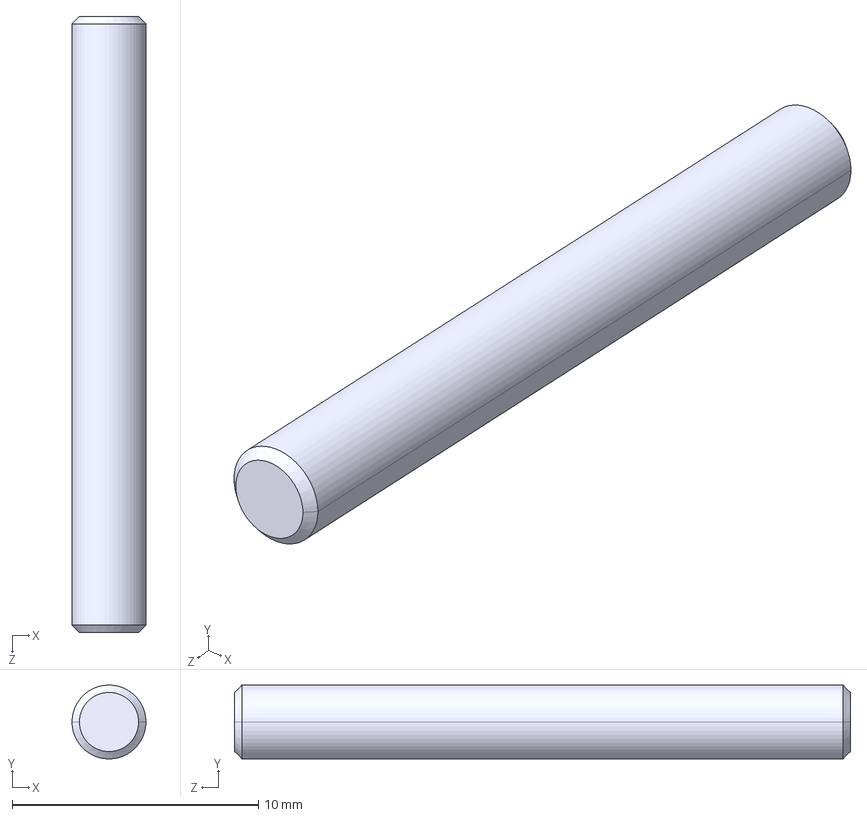
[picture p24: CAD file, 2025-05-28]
STEP/dowel_pin_custom_M3x25.STEP
3.00 x 3.00 x 25.0 mm

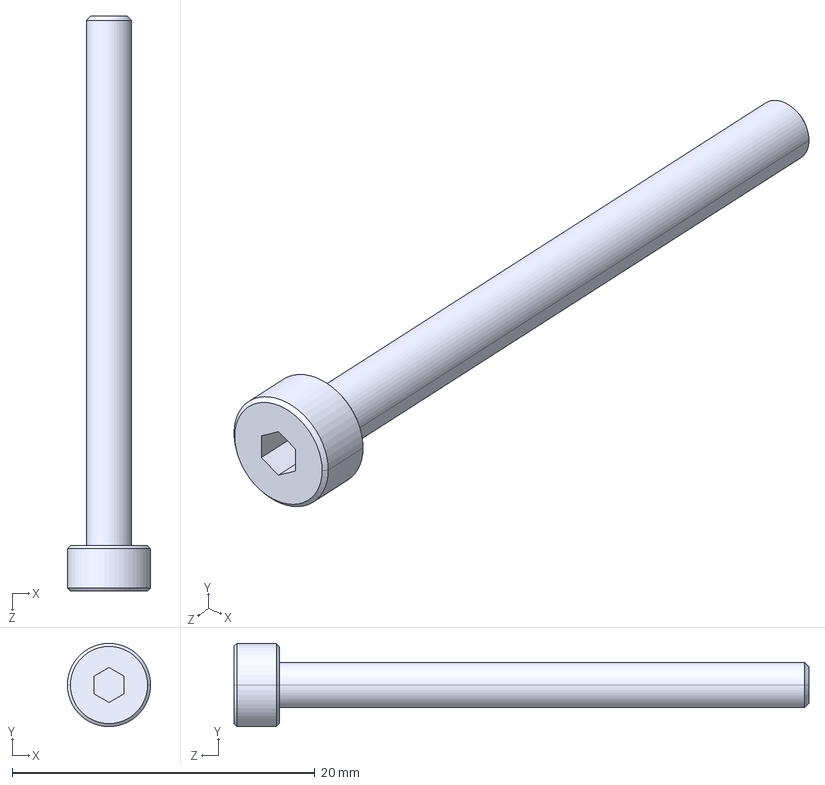
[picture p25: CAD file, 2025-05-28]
STEP/hex_m3_custom_socketcap_35mm.STEP
5.50 x 5.50 x 38.0 mm

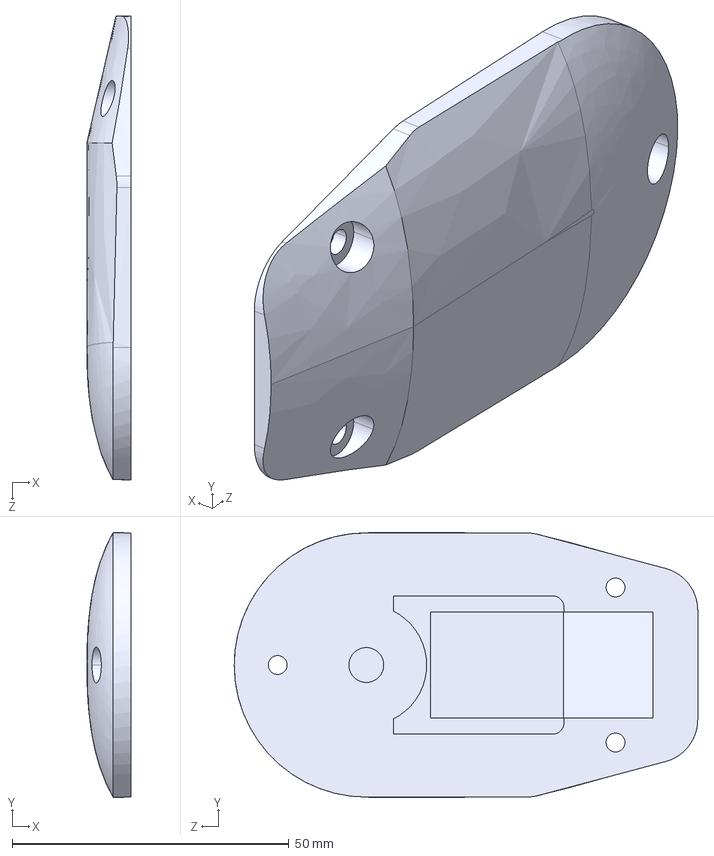
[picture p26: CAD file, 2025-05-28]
STEP/Upper_arm_part3.STEP
8.00 x 47.8 x 83.7 mm

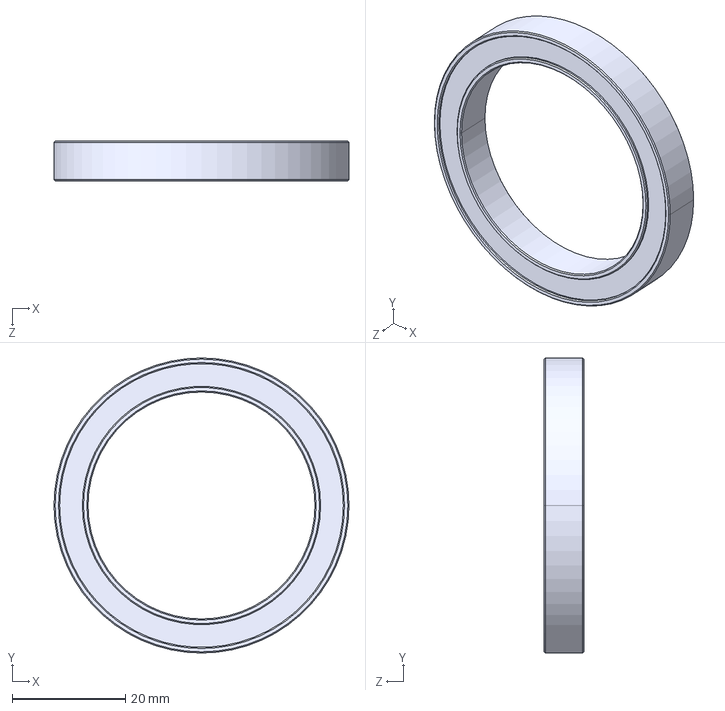
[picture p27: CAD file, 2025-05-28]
STEP/roulement_40x52x7.STEP
52.0 x 52.0 x 7.00 mm

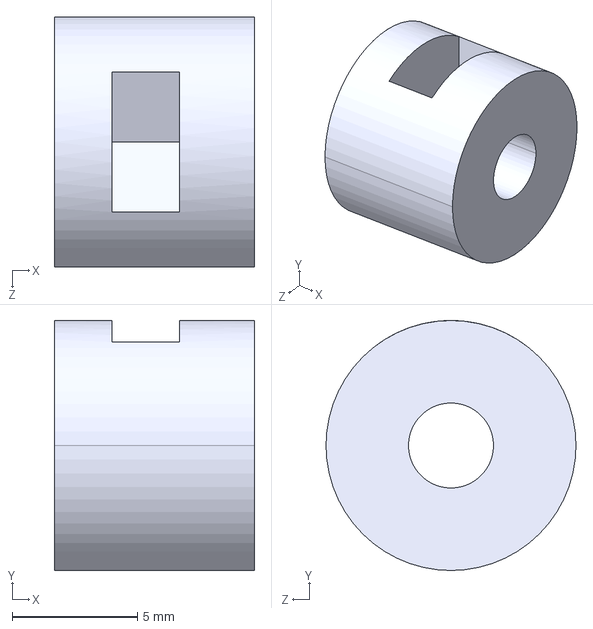
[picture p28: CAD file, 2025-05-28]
STEP/pulley_default.STEP
8.00 x 10.0 x 10.0 mm

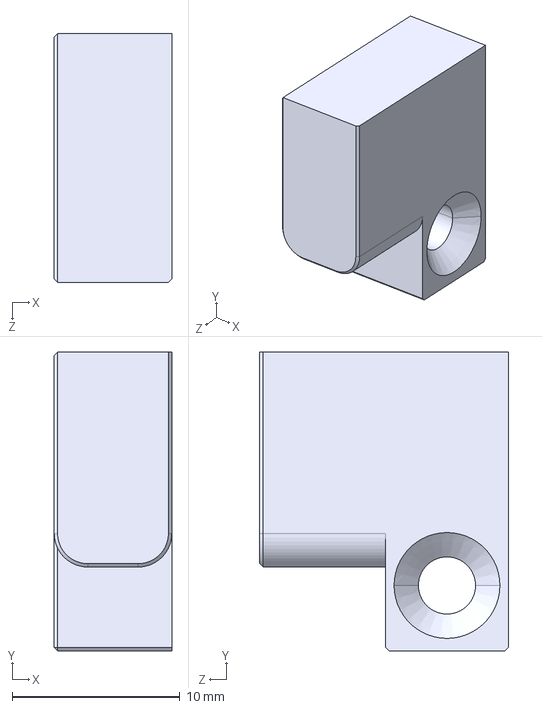
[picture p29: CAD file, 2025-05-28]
STEP/wire_cover_base_default.STEP
7.00 x 17.8 x 14.8 mm

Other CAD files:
STEP/Main_link_elbow.STEP
STEP/ASM, Amass MR30 mated pair_default.STEP
STEP/Main_link_upper_arm.STEP
STEP/Cycloid_drive_upper_arm.STEP
STEP/Amass MR30-FB_default_default.STEP
STEP/Amass MR30-M_default_default.STEP
STEP/Amass MR30-shroud_default_default.STEP
STEP/Base_default.STEP
STEP/Bionic_arm.STEP
STEP/Cycloid_drive_default.STEP
STEP/Cycloid_drive_fore_arm.STEP
STEP/Cycloid_drive_housing_rotation.STEP
STEP/Elbow_default.STEP
STEP/Hand_default.STEP
STEP/Middle_upper_arm_default.STEP
STEP/RoaringTop_2200mah_default.STEP
STEP/Shoulder_default.STEP
STEP/Upper_arm_elbow_part2.STEP
STEP/Upper_arm_part1.STEP
STEP/Upper_arm_part2.STEP
STEP/WaveShare_Bus_Servo_DriverBoard_Défaut.STEP
STEP/Wrist_default.STEP
STEP/XT60_male_connector_default.STEP
STEP/base_axis_default.STEP
STEP/base_housing_default.STEP
STEP/bearing_shaft_default.STEP
STEP/bracket_30x30_default.STEP
STEP/cable_pulley_base.STEP
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

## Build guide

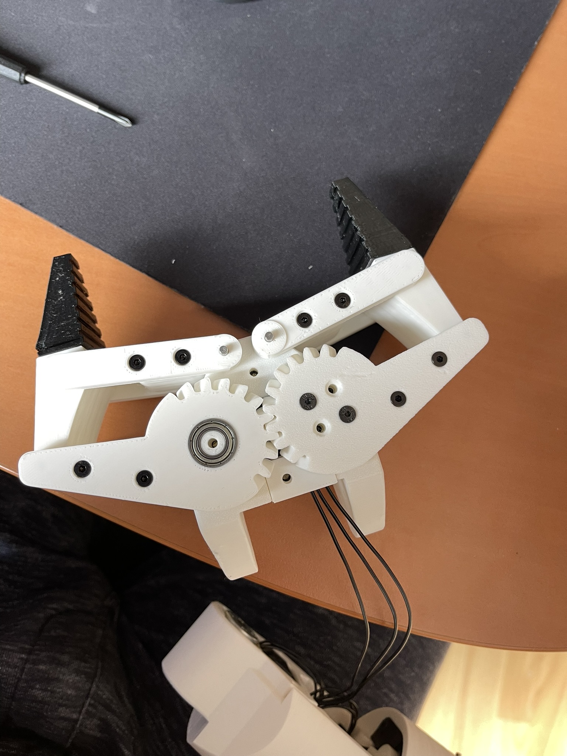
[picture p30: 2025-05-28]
media/assembly/IMG_1366.JPEG

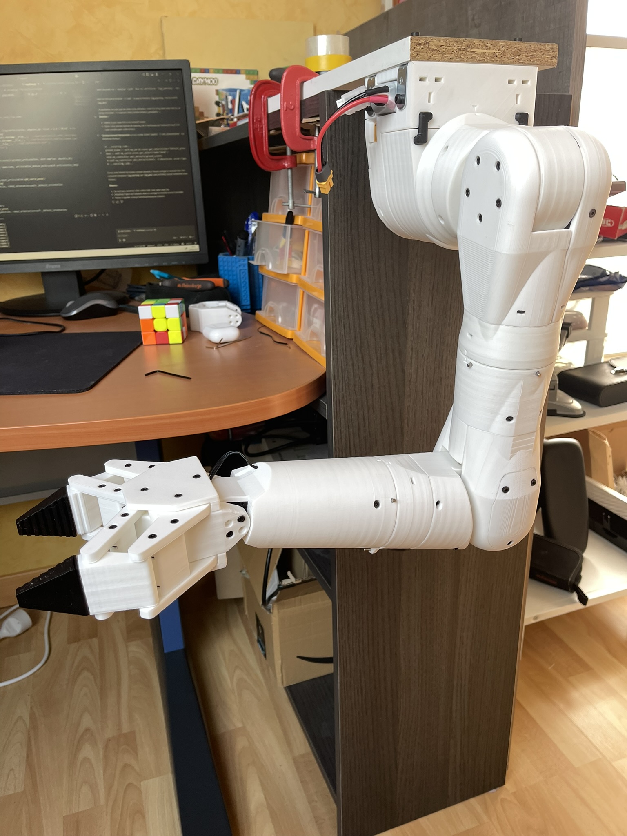
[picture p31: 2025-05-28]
media/assembly/Full_arm_iso.JPEG

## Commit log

2025-03-31 Step part1
    [ASM, Amass MR30 mated pair_default.STEP, Amass MR30-FB_default_default.STEP, Amass MR30-M_default_default.STEP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]
2025-05-28 Step and BOM v1.0
    [ASM, Amass MR30 mated pair_default.STEP, Amass MR30-FB_default_default.STEP, Amass MR30-M_default_default.STEP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]
